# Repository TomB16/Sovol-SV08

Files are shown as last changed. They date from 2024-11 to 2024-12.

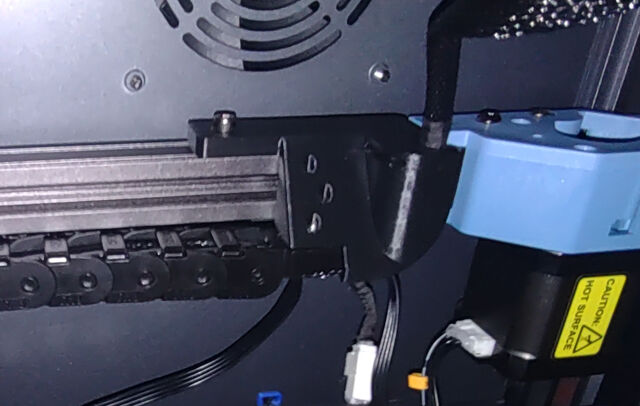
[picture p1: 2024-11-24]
Components/Energy Chain to Gantry/chain-fitting_resized_640p.jpg

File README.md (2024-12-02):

I've included my SV08 configs for anyone who wants a starting place.  The configs supplied with the SV08 are essentially unusable.  These configs have printed a ton of stuff.  I have two SV08 and they are working about 50% of the time.

Many in the Sovol community prefer mainline klipper.  It can be installed using the excellent resource at: https://github.com/Rappetor/Sovol-SV08-Mainline

Here is how I bring up an SV08, once it has new firmware.

- PROBE_CALIBRATE
- Print the Layer 1 test (15mm disk).  This will use roughly 11mm of filament per print.  Slice it with one layer, one loop, skirt.
  - Peel the skirt from the build plate and measure with a caliper.  The thickness should be whatever you sliced.
  - Adjust the Z offset using [Sliced layer height - measured layer height]

That should get you pretty close.  Once you are laying down a nice first layer, it's down to standard tuning.  There is a ton of Klipper tuning resource on the net.

Notes:

- The Sovol bed sensor is temperature sensitive and there is also significant thermal bed movement.  Because of this, these macros heat soak for a significant period of time (minimum 2, max 12 minutes, depending on toolhead temperature).  When the printer is being used, it will do minimal heat soak.  Feel free to adjust to taste.
- I have two SV08 received roughly two months apart.  The second one has a toolhead that runs 8*C cooler than the first.  Perhaps they used a different fan or slightly different duct.  Because of this, I set the two printers differently:  variable_heat_soak_temp = 42 (on printer 1), 36 (on printer 2).  I suspect a good number to start with would be the ultimate temperature your print head reaches after printing for hours minus 10C.
- If you change your bed sensor, you will want to completely rejigger this heat soak.  If you use a stock sensor, you will lay down an accurate first layer every time but it does a lot of heat soak on a cold printer before printing.
- My printers are both 100% stock hardware, including the inductive bed sensor.  I have completely taken over the software, however.
- After 3 months with the first printer, I am extremely pleased with the SV08.  I've squeezed about 20Kg of plastic through the two printers in that time.  Early on, there were quite a few failures.  Once the config was at a decent point and the Orca Profile was reasonably well tuned, I don't recall having a failure.  The stock Sovol build plate is brilliant.  I print 99% PLA.

Happy printing.

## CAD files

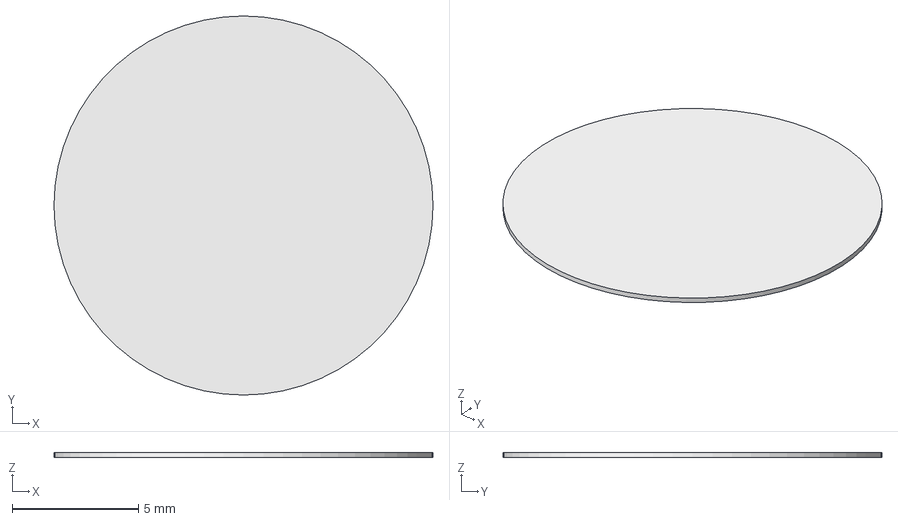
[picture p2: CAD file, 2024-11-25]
Calibration/Layer 1/Layer 1 Circle 15mm v0.01.step
15.0 x 15.0 x 0.2 mm

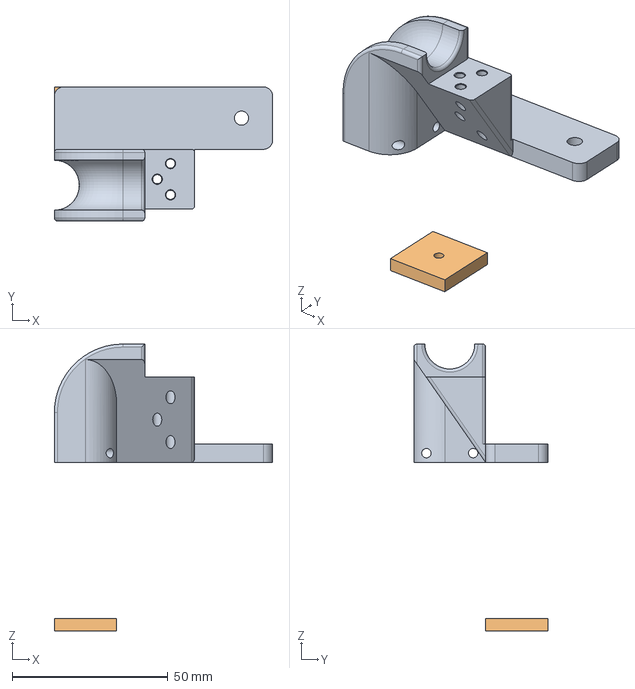
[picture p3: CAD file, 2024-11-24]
Components/Energy Chain to Gantry/Energy Chain to Gantry v0.02.FCStd
70.0 x 43.0 x 92.0 mm
BodyReceiver
BodyTest

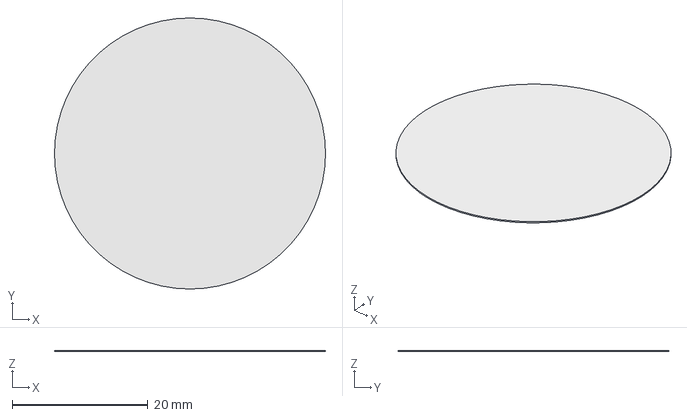
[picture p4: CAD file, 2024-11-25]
Calibration/Layer 1/Layer 1 Circle 40mm v0.01.step
40.0 x 40.0 x 0.2 mm

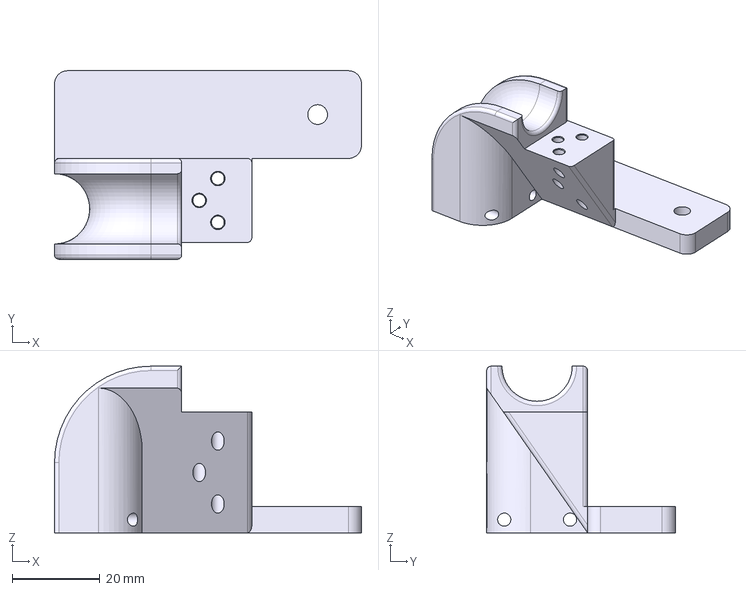
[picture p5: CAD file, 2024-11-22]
Components/Energy Chain to Gantry/Energy Chain to Gantry v0.02-BodyReceiver.step
70.0 x 43.0 x 38.0 mm

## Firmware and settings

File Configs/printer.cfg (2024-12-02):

[include mainsail.cfg]
[include sovol-macros.cfg]
[include KAMP_Purge.cfg]
[include timelapse.cfg] # DONT FORGET TO INSTALL THE TIMELAPSE PLUGIN

# PLEASE UNCOMMENT THE FILE THAT BEST FITS YOUR CONFIGURATION

# IF YOU ARE USING THE SCREEN THAT COMES WITH THE SV08
[include options/lcd/*.cfg]

# Choose whether you would rather control your LEDs with the LCD screen or KlipperScreen
# THESE ARE INCOMPATIBLE WITH EACH OTHER; ONLY ENABLE ONE
[include options/led/lcd.cfg]
#[include options/led/hdmi.cfg]

# If you are using the stock probe, keep the following lines as-is.
# If you have an Eddy probe, comment the first and uncomment the second,
# then go read options/probe/eddy.cfg. 
# Also, when using eddy, comment out/remove the [probe] section here in the printer.cfg
[include options/probe/stock.cfg]
#[include options/probe/eddy.cfg]

[mcu]
serial: /dev/serial/by-id/usb-Klipper_stm32f103xe_<UUID>-if00
restart_method: command     

[mcu extra_mcu]
serial: /dev/serial/by-id/usb-Klipper_stm32f103xe_<UUID>-if00
restart_method: command      

[virtual_sdcard]
path: ~/printer_data/gcodes
on_error_gcode: CANCEL_PRINT

[printer]
kinematics: corexy           
max_velocity: 700           
max_accel: 8500          
#max_accel_to_decel: 10000 # deprecated
minimum_cruise_ratio: 0.5
max_z_velocity: 20           
max_z_accel: 500             
square_corner_velocity: 5.0 

[stepper_x]
step_pin: PE2
dir_pin: !PE0
enable_pin: !PE3
rotation_distance: 40         
microsteps: 16                
full_steps_per_rotation:200   
endstop_pin: tmc2209_stepper_x: virtual_endstop              
position_min: 0               
position_endstop: 355         
position_max: 355             
homing_speed: 30              
homing_retract_dist: 0        
homing_positive_dir: True     
#--------------------------------------------------------------------
[tmc2209 stepper_x]
uart_pin: PE1
interpolate: True             
run_current: 1.1              
#hold_current: 1.2             
sense_resistor: 0.150         
stealthchop_threshold: 0      
uart_address:3
driver_sgthrs: 70
diag_pin: PE15

[stepper_y]
step_pin: PB8
dir_pin: !PB6
enable_pin: !PB9
rotation_distance: 40         
microsteps: 16                
full_steps_per_rotation:200   
endstop_pin: tmc2209_stepper_y: virtual_endstop              
position_min: 0               
position_endstop: 364         
position_max: 364            
homing_speed: 30              
homing_retract_dist: 0        
homing_positive_dir: true     
#--------------------------------------------------------------------
[tmc2209 stepper_y]
uart_pin: PB7
interpolate: True             
run_current: 1.1              
#hold_current: 1.2             
sense_resistor: 0.150         
stealthchop_threshold: 0      
uart_address:3
driver_sgthrs: 70
diag_pin: PE13 

[stepper_z] #motherboard：Z3 
step_pin:PC0    
dir_pin:PE5    
enable_pin:!PC1    
rotation_distance: 40         
gear_ratio: 80:12             
microsteps: 16                
endstop_pin: probe:z_virtual_endstop           
position_max: 347             
position_min: -5              
#position_endstop: 0
homing_speed: 15.0
homing_retract_dist: 5.0
homing_retract_speed: 15.0
second_homing_speed: 10.0

[tmc2209 stepper_z]
uart_pin: PE6 
interpolate: true             
run_current: 0.55           
#hold_current: 0.58         
sense_resistor: 0.150         
stealthchop_threshold: 999999 
uart_address:3

[stepper_z1] ##motherboard：Z1
step_pin:PD3  
dir_pin:!PD1 
enable_pin:!PD4 
rotation_distance: 40         
gear_ratio: 80:12            
microsteps: 16               

[tmc2209 stepper_z1]
uart_pin:PD2  
interpolate: true             
run_current:  0.55          
#hold_current: 0.58           
sense_resistor: 0.150         
stealthchop_threshold: 999999 
uart_address:3

[stepper_z2] ##motherboard：Z2
step_pin:PD7
dir_pin:PD5   
enable_pin:!PB5
rotation_distance: 40         
gear_ratio: 80:12             
microsteps: 16                

[tmc2209 stepper_z2]
uart_pin:PD6  
interpolate: true             
run_current: 0.55            
#hold_current: 0.58           
sense_resistor: 0.150         
stealthchop_threshold: 999999 
uart_address:3

[stepper_z3] ##motherboard：Z4
step_pin:PD11 
dir_pin:!PD9 
enable_pin:!PD12   
rotation_distance: 40         
gear_ratio: 80:12             
microsteps: 16                

[tmc2209 stepper_z3]
uart_pin:PD10    
interpolate: true            
run_current: 0.55         
#hold_current: 0.58           
sense_resistor: 0.150         
uart_address:3
stealthchop_threshold: 999999 

[thermistor my_thermistor_e]
temperature1:25
resistance1:110000
temperature2:100
resistance2:7008
temperature3:220
resistance3:435

[extruder]
step_pin: extra_mcu:PA8   
dir_pin: extra_mcu:PB8    
enable_pin:!extra_mcu: PB11   
rotation_distance: 6.5 
microsteps: 16                
full_steps_per_rotation: 200 
nozzle_diameter: 0.400        
filament_diameter: 1.75  
max_extrude_only_distance: 150   
max_extrude_cross_section: 5
heater_pin:extra_mcu:PB9  
sensor_type:my_thermistor_e  
pullup_resistor: 11500
sensor_pin: extra_mcu:PA5  
min_temp: 5                  
max_temp: 305                 
max_power: 1.0                
min_extrude_temp: 5
control : pid
pid_kp : 33.838
pid_ki : 5.223
pid_kd : 47.752
pressure_advance: 0.025       
pressure_advance_smooth_time: 0.035    

[tmc2209 extruder]
uart_pin: extra_mcu:PB10  
interpolate: True             
run_current: 0.8           
#hold_current: 0.75             
uart_address:3
sense_resistor: 0.150          

[verify_heater extruder]      
max_error: 120                
check_gain_time:30           
hysteresis: 5                
heating_gain: 2               

[filament_switch_sensor filament_sensor]
pause_on_runout: True
event_delay: 3.0
pause_delay: 0.5
switch_pin: PE9

[thermistor my_thermistor]
temperature1:25
resistance1:100000
temperature2:50
resistance2:18085.4
temperature3:100
resistance3:5362.6

[heater_bed]
heater_pin:PA0
sensor_type: my_thermistor  
sensor_pin: PC5
max_power: 1.0               
min_temp: 5                  
max_temp: 105                
control : pid
pid_kp : 73.571
pid_ki : 1.820
pid_kd : 783.849

[verify_heater heater_bed]      
max_error: 120                
check_gain_time:40           
hysteresis: 5                
heating_gain: 2 

# PLEASE REMOVE THIS WHEN USING EDDY
[probe]
#z_offset: 0

[probe_pressure]
pin: ^!PE12     
x_offset: 0                  
y_offset: 0
z_offset : 0
speed: 1.0

[quad_gantry_level]          
gantry_corners:              
	-60,-10
	410,420
points:
	36,10
	36,320
	346,320
	346,10
speed: 400                   
horizontal_move_z: 10       
retry_tolerance: 0.05      
retries: 5                  
max_adjust: 30   

[multi_pin print_cooling_fan_pins]
pins: extra_mcu:PA7, extra_mcu:PB1

# print/part cooling fan
[fan]
pin: multi_pin:print_cooling_fan_pins
max_power: 1.0

[fan_generic exhaust_fan] # exhaust fan
pin: PA2
max_power: 1.0

# MCU fan, aka noisy boi, is now only enabled when using steppers, extruder, heatbed; 5min timeout
[controller_fan MCU_fan]
pin: PA1
max_power: 1
kick_start_time: 0.5
fan_speed: 1
idle_timeout: 300
heater: extruder, heater_bed
stepper: stepper_x, stepper_y

# Want your fan (host) temperature controlled? Uncomment the next section and comment out the above section, derived from: https://www.reddit.com/r/Sovol/comments/1cqntzu/first_mod_on_my_sv08_noctua_fan_for_the/
# WARNING: Do you have a Noctua 24V 4010 fan (eg. NF-A4x10 24V PWM)? Then this will not work and results in a non-spinning fan.
# In that case you can either use the above 'controller_fan' section or use 'control: watermark' and leave the pid entries commented out.
#[temperature_fan MCU_fan]
#pin: PA1
#kick_start_time: 0.5
#max_power: 1.0
#min_temp: 0
#max_temp: 90
#hardware_pwm: true
#target_temp: 50
#sensor_type: temperature_host # please comment out or remove the [temperature_sensor Host_temp] section if you don't want the temperature shown twice in the interface.
#max_speed: 1.0
#min_speed: 0.1
#control: pid
#pid_Kp: 2.0     ;40
#pid_Ki: 5.0     ;0.2
#pid_Kd: 0.5     ;0.1
#pid_deriv_time: 2.0
#control: watermark # use this control if pid control does not work for your fan

[heater_fan hotend_fan]      
pin: extra_mcu:PA6   
max_power: 1.0               
kick_start_time: 0.5         
heater: extruder             
heater_temp: 50              
tachometer_pin:extra_mcu:PA1
tachometer_ppr: 1
tachometer_poll_interval: 0.0013

[gcode_arcs]                       
resolution: 1.0                    

[idle_timeout]
gcode: _IDLE_TIMEOUT
timeout: 600

[temperature_sensor mcu_temp]         
sensor_type: temperature_mcu
min_temp:0
max_temp:100

[temperature_sensor Host_temp]     
sensor_type: temperature_host
min_temp: 0
max_temp: 110

[temperature_sensor Toolhead_Temp]
sensor_type: temperature_mcu
sensor_mcu: extra_mcu

[pause_resume]

[exclude_object]

[adxl345]
cs_pin:extra_mcu:PB12
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

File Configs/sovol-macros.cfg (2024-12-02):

# mainled macros defined in options/led/*

[force_move]
enable_force_move: True

[gcode_macro _global_var]
variable_pause_park:{'x': 0, 'y': 0, 'z': 10, 'e': 1}
variable_cancel_park:{'x': 0, 'y': 350, 'z': 10, 'e': 1}
variable_z_maximum_lifting_distance: 345
variable_pause_resume_travel_speed: 150
variable_bed_mesh_calibrate_target_temp: 65
variable_load_filament_extruder_temp: 200
variable_heat_soak_min: 2 # in minutes
variable_heat_soak_temp: 42 # celcius
variable_heat_soak_multiplier: 2 # time multiplier
variable_heat_soak_max: 12 # in minutes
variable_cool_down_time: 2 # in minutes
gcode:

[gcode_macro PRINT_START]
description: 
variable_state: 'Prepare'
variable_record_extruder_temp:0
variable_max_record_extruder_temp:0
gcode:
    {% set bedtemp = params.BED_TEMP|default(60)|int %}
    {% set hotendtemp = params.EXTRUDER_TEMP|default(230)|int %}
    {% set heatsoak = params.HEATSOAK|default(True)|int %}
    {% set heatsoak_min = printer['gcode_macro _global_var'].heat_soak_min|default(2)|int %} # takes heatsoak minimum from global variables
    {% set heatsoak_temp = printer['gcode_macro _global_var'].heat_soak_temp|default(40)|int %}
    {% set heatsoak_time = heatsoak_min |int %}
    {% set heatsoak_multiplier = printer['gcode_macro _global_var'].heat_soak_multiplier|default(1.5)|float %}
    {% set heatsoak_max = printer['gcode_macro _global_var'].heat_soak_max|default(10)|int %}
    {% set mesh_name = "default" %}
    {% set mesh_calibrate_temp = printer['gcode_macro _global_var'].bed_mesh_calibrate_target_temp|int %}

    {% set extruder_target_temp = 125 %}

    {% set bed_target_temp = bedtemp|int %}



    M400

    CLEAR_PAUSE

    # set minimum temperature to heat to mesh calibrate temperature
    {% if bed_target_temp <= mesh_calibrate_temp %}
        {% set bed_target_temp = mesh_calibrate_temp %}
    {% endif %}

    G90

    M140 S{bed_target_temp}
    {% if state == 'Prepare' %}

        # check for filament

        {% if printer['filament_switch_sensor filament_sensor'].enable == True and
              printer['filament_switch_sensor filament_sensor'].filament_detected != True
        %}
            M117 Insert filament
            { action_respond_info("Insert filament.") }
            CANCEL_PRINT
        {% endif %}

        # calculate heat soak time

        {% set heatsoak = True %}
        {% set toolhead = printer["temperature_sensor Toolhead_Temp"] %}
        {% if toolhead.temperature < heatsoak_temp %}
            {% set heatsoak_time = ((heatsoak_temp - toolhead.temperature) * heatsoak_multiplier) + heatsoak_min |int %}
            {% if heatsoak_time > heatsoak_max %}  {% set heatsoak_time = heatsoak_max %}  {% endif %}
            { action_respond_info("Cold start heat soak.  Current toolhead temp %.2f.  Delay %i min." % (toolhead.temperature, heatsoak_time)) }
        {% else %}
            { action_respond_info("Hot printer.  Minimum heat soak.  Current toolhead temp %.2f.  Delay %i min." % (toolhead.temperature, heatsoak_time)) }
        {% endif %}

        {% if printer.extruder.temperature < extruder_target_temp %}
            M117 Pre-heat extruder
            #{ action_respond_info("Pre-heat extruder.") }
            M109 S{extruder_target_temp} 
        {% endif %}


        #Start exhaust fan
        #SET_FAN_SPEED FAN=exhaust_fan SPEED=1

        {action_respond_info("Extruder Heating to %iC." % (extruder_target_temp))}
        M104 S{extruder_target_temp}

        {% if printer.heater_bed.temperature < bed_target_temp %}
            M117 Bed heating
            { action_respond_info("Bed heating.") }
            M190 S{bed_target_temp}
        {% endif %}
       
        {% if heatsoak == True %}
          M117 Heat soak
          { action_respond_info("Heat soak delay %i." % (heatsoak_time)) }
          G4 P{heatsoak_time * 60000} # pause for x number of minute(s) (see variable_heat_soak_time)
        {% endif %}

        {% if printer.toolhead.homed_axes|lower != "xyz" %}
            M117 Home
            { action_respond_info("Home.") }
            G28
        {% endif %}
        
        {% if printer.quad_gantry_level.applied|lower != 'true' %}
            M117 QGL
            { action_respond_info("QGL.") }
            QUAD_GANTRY_LEVEL
            M117 Home Z after QGL
            { action_respond_info("Home Z after QGL.") }
            G28 Z # And once again after QGL, important..
            # M117 Auto Z Offset
            # Z_OFFSET_CALIBRATION
        {% endif %}
        
        M117 Bed mesh adaptive
        { action_respond_info("Bed mesh adaptive.") }
        BED_MESH_CALIBRATE ADAPTIVE=1 

        # Set final temperatures before printing instead of relying on the OrcaSlicer start gcode..
        M117 Final heat
        { action_respond_info("Final heat.") }
        M140 S{bedtemp} ;set bed temp
        M104 S{hotendtemp} ;set extruder temp
        M190 S{bedtemp} ;wait for bed temp
        M109 S{hotendtemp};wait for extruder temp

        FILAMENT_PURGE
        
        SET_GCODE_VARIABLE MACRO=PRINT_START VARIABLE=state VALUE='"Start"' 
        UPDATE_DELAYED_GCODE ID=_print_start_wait DURATION=0.5

    {% elif state == 'Start' %}
        M117 Printing
        {action_respond_info("Printing.")}
    {% endif %}
    
[gcode_macro PRINT_END]
description: 
variable_state: 'normal'
gcode:
    {% set z_max = printer['gcode_macro _global_var'].z_maximum_lifting_distance|int %}
    {% set e_mintemp  = printer.configfile.settings['extruder'].min_extrude_temp %}
    {% set cooldown_time = printer['gcode_macro _global_var'].cool_down_time|default(3)|int %}

    M400
    SET_GCODE_VARIABLE MACRO=PRINT_START VARIABLE=state VALUE='"Prepare"'
    SET_GCODE_VARIABLE MACRO=PRINT_START VARIABLE=record_extruder_temp VALUE=0  
    SET_GCODE_VARIABLE MACRO=PRINT_START VARIABLE=max_record_extruder_temp VALUE=0

    M117 Finish Print!!!
    G91
    {% if printer['filament_switch_sensor filament_sensor'].enable == True and
          printer['filament_switch_sensor filament_sensor'].filament_detected == True
    %}
        {% if (printer.extruder.target != 0 and printer.extruder.temperature >= printer.extruder.target) or
              printer.extruder.temperature >= e_mintemp
        %}
            G1 E-25 F2700
            G1 E-2 Z0.2 F2400
        {% endif %}
    {% endif %}

    {% if (printer.gcode_move.position.z + 25) < z_max %}
        G1 Z+25 F3000
    {% else %}
        G1 Z+{(z_max - printer.gcode_move.position.z)} F3000
    {% endif %}
    G90
    G1 X0 Y360 F9000

    _ALL_FAN_OFF
    TURN_OFF_HEATERS

    M84 X Y Z E  

    M220 S100
    M221 S100

    CLEAR_PAUSE

    {action_respond_info("Finish Print!")}

    {action_respond_info("Ventilating Enclosure for %i min." % cooldown_time)}
    SET_FAN_SPEED FAN=exhaust_fan SPEED=1
    G4 P{cooldown_time * 60000}
    SET_FAN_SPEED FAN=exhaust_fan SPEED=0
    {action_respond_info("Ventilation complete.")}

[gcode_macro _IDLE_TIMEOUT]
gcode:
    {% if printer.print_stats.state == "paused" %}
      RESPOND TYPE=echo MSG="No operations in 10min!"
    {% else %}
     M84
     TURN_OFF_HEATERS
    {% endif %}

[delayed_gcode exhaust_fan_off]
gcode:
    SET_FAN_SPEED FAN=exhaust_fan SPEED=0

[gcode_macro _ALL_FAN_OFF]
gcode:
    M106 S0
    # Run the exhaust fan for another 2min after the other fans and then turn it off
    # UPDATE_DELAYED_GCODE ID=exhaust_fan_off DURATION=120
    M107

[gcode_macro CLEAN_NOZZLE] 
gcode:
    {% if printer.toolhead.homed_axes != "xyz" %}
       G28
    {% endif %}
    G90 
    G1 X348 Y0 Z0.3 F9000
    M117 Nozzle heating...
    M109 S200
    G91
    G1 Z10 F300
    G90
    M106 S255
    M104 S130
    M117 Clean nozzle
    G1 X315 Y360 F9000
    G1 Z0.2 F300
    G1 X352 F4500
    G1 Y360 X324
    G1 Y360 X345
    G1 Y360 X324
    G1 Y360 X345
    G1 Y360 X324
    G1 Y360 X345
    G1 Y360 X324
    G1 Y360 X345
    G1 Y360 X324
    G1 Y360 X325
    G1 Y356 X324 Z5
    G1 Z0.2
    G1 Y360 X324
    G1 Y357 X326
    G1 Y360 X326
    G1 Y357 X328
    G1 Y360 X330
    G1 Y357 X332
    G1 Y360 X334
    G1 Y357 X336
    G1 Y360 X338
    G1 Y357 X340
    G1 Y360 X324
    G1 Y357 X326
    G1 Y360 X326
    G1 Y357 X328
    G1 Y360 X330
    G1 Y357 X332
    G1 Y360 X334
    G1 Y357 X336
    G1 Y360 X338
    G1 Y357 X340
    G1 Y360 X324
    G1 Y357 X326
    G1 Y360 X326
    G1 Y357 X328
    G1 Y360 X330
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
    M117 Finished cleaning
    M109 S130
    M107 
    G91
    G1 Z10 F300
    G90
    G28 Z0

# Bring the nozzle to the center of the bed
[gcode_macro CENTER]
gcode:
    G0  X175 Y175 F5000

[gcode_macro _CALIBRATION_ZOFFSET]
gcode:
    M117 Calibrate Offset
    QUAD_GANTRY_LEVEL
    M140 S65
    G4 P500
    CLEAN_NOZZLE
    G4 P500
    M117 Z-offset calibration
    Z_OFFSET_CALIBRATION
    Z_OFFSET_APPLY_PROBE
    SAVE_CONFIG 

[delayed_gcode _auto_zoffset]
gcode:
    SAVE_VARIABLE VARIABLE=offsetadjust VALUE={'%05.2f' % (0)}
    _CALIBRATION_ZOFFSET
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
